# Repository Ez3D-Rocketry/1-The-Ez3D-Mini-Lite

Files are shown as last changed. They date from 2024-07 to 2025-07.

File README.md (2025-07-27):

# The-Ez3D-Mini-Lite

- Great park flyer that uses mini A motors
- Parts tape together
- No glue required

# Parts List:
1. Ez3D-1320 Fin Can
2. BT-20 Nose Cone
3. 13mm Retainer Cap
   - Print out the multiple sizes (No scaling, +3%, +5%), These account for different printing tolerances and post-flight shrinking.
4. Six (6) inches of BT-20 type body tube
   - A standard 18 inch tube makes three kits
   - 3D printable tube cutting guide included in repository files
5. Three (3) feet of Kevlar string for Recovery Harness
   - Flight tested on 9KM DWLIFE Black Braided Kevlar Cord (1.3mm, 300 lb) but others may work
6. Twelve (12) inches of streamer (Optional)
8. Tape

# Assembly: 

**NOTE: Individual printers and filament have different tolerances** <br />
**- Fit check items before assembly and sand to fit if required**
     
1. Tie Recovery Harness to hole in Fin Can
2. Thread Recovery Harness thru Body Tube
3. Slide Body Tube onto top of Fin Can
4. Tape Body Tube to Fin Can - avoid blocking integrated launch lug
5. Tie loose end of Recovery Harness to Nose Cone
6. Tie streamer to Recovery Harness near top of Nose Cone



# Launch Preparation:
1. Insert 1 or 2 squares of recovery wadding into Body Tube
2. Load Recovery Harness and Streamer into Body Tube
3. Place Nose Cone on top of Body Tube - ensure slightly snug fit
4. Slide BT-5 insulator into Fin Can before motor (Optional)
5. Load motor into Fin Can
6. Screw Motor Retention Cap onto base of Fin Can
   - Depending on your printer, the larger sizes may fit better
   - After a flight or two, the smaller size may fit better
7. Launch using standard model rocket procedures

# Recommended motors and expected performance: 

1/2A3-2T or 4T   = 170 ft  (Optimum delay = 2.9 s)

A10-3T               = 370 ft (Optimum delay = 3.5 s)

A3-4T                = 400 ft (Optimum delay = 3.9 s)

# IMPORTANT POST FLIGHT NOTES:
- 3D printed material shrinks after cooling down from heat of motor
- Removal of motor may be difficult or impossible after one or several flights
- The smaller motor retainer cap may fit better after the first flight
- If existing motor retainer caps no longer work, friction or tape may suffice for retention
- PLA filament most suspectable to shrinking. Others may last longer.

## Entire kit fits in a Ziplock sandwich bag!



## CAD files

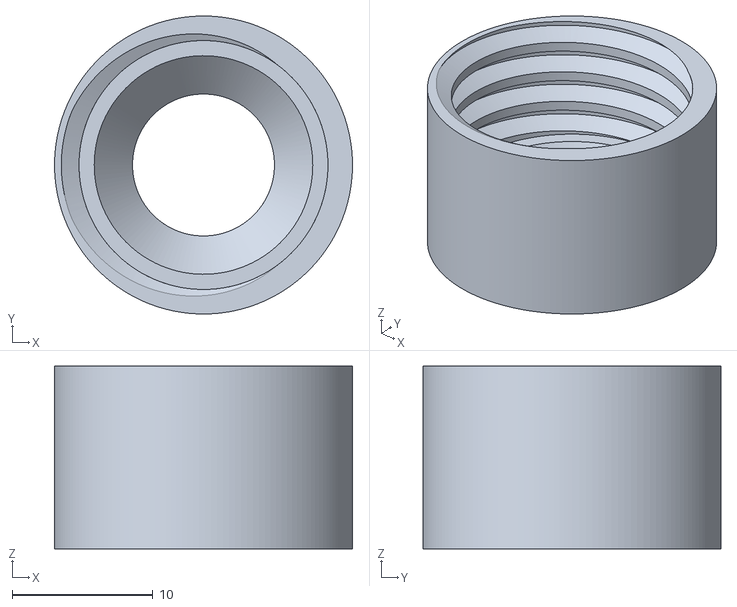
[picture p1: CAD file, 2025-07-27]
3D printing files/13mm Retainer Cap M20x2-13mmTall x1.01in X and Y.stl
21.2 x 21.2 x 13.0

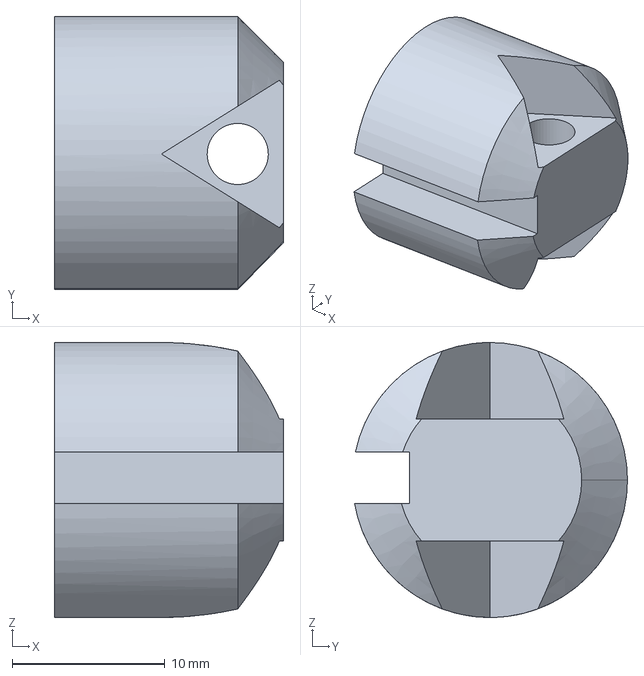
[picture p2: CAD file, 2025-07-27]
FreeCAD Files/BT20 Nose Cone - Elliptical, Solid, with slot.FCStd
15.0 x 17.9 x 18.0 mm

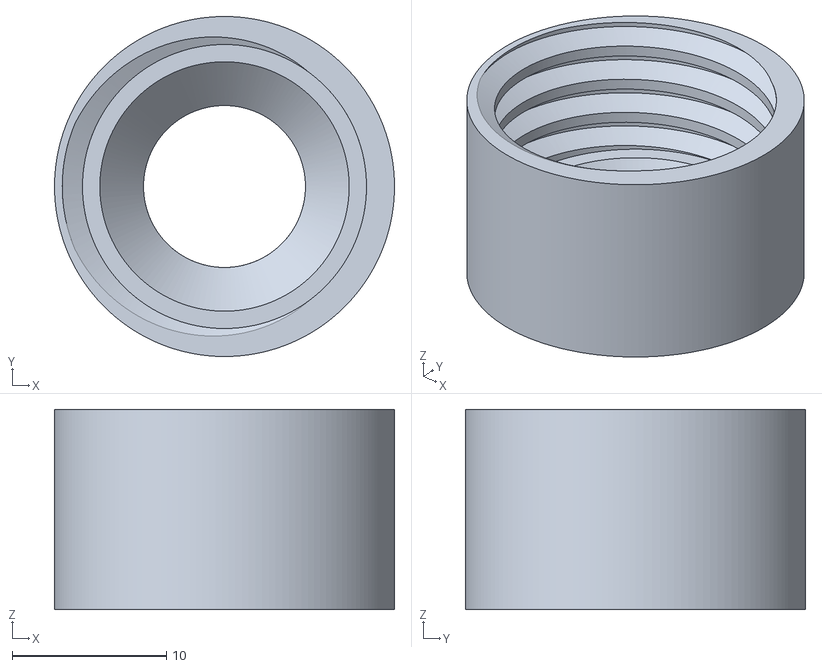
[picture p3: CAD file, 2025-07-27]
3D printing files/13mm Retainer Cap M20x2-13mmTall x1.05 in X and Y.stl
22.0 x 22.0 x 13.0

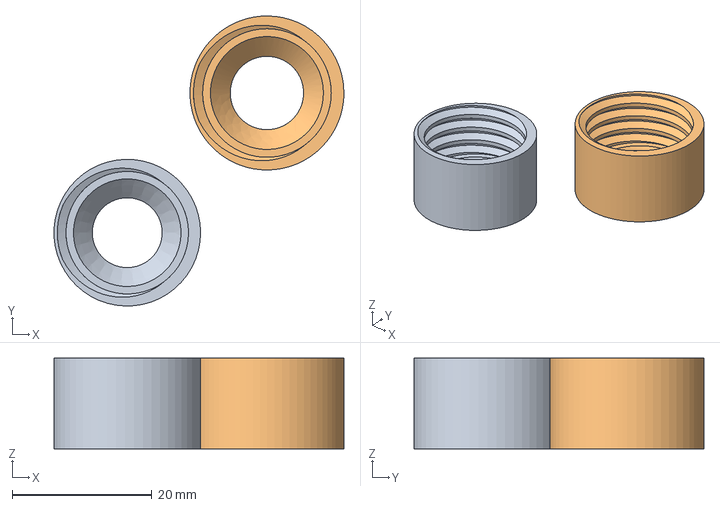
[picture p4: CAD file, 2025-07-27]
FreeCAD Files/13mm Retainer Cap M20x2-13mmTall.FCStd
41.5 x 41.5 x 13.0 mm
Use this Clone to make scaled up versions

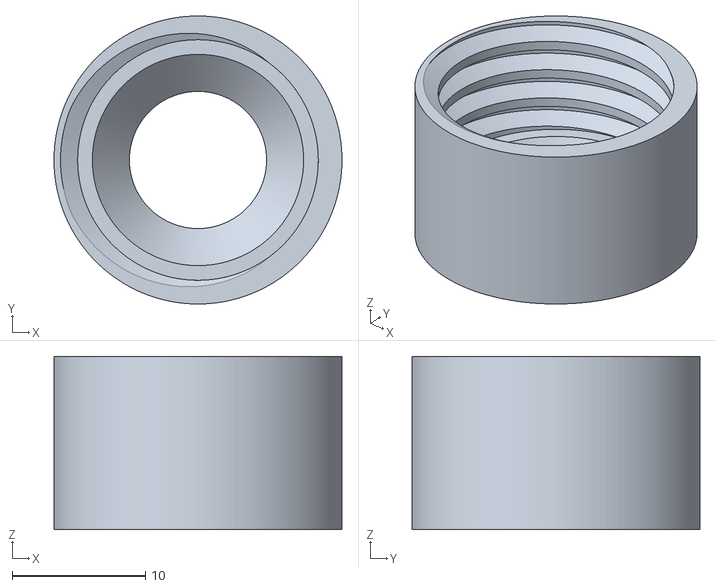
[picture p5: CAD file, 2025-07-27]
3D printing files/13mm Retainer Cap M20x2-13mmTall x1.03 in X and Y.stl
21.6 x 21.6 x 13.0

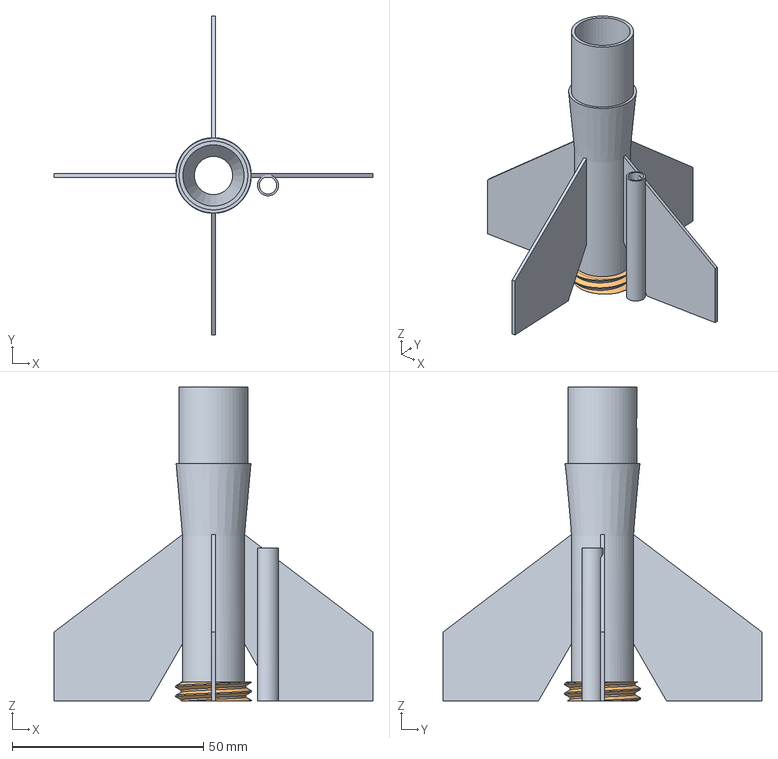
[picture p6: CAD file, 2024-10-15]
FreeCAD Files/Ez3D-1320-4 Fin Can.FCStd
83.5 x 83.5 x 82.1 mm
13mmThread20x2.5-5mmTall

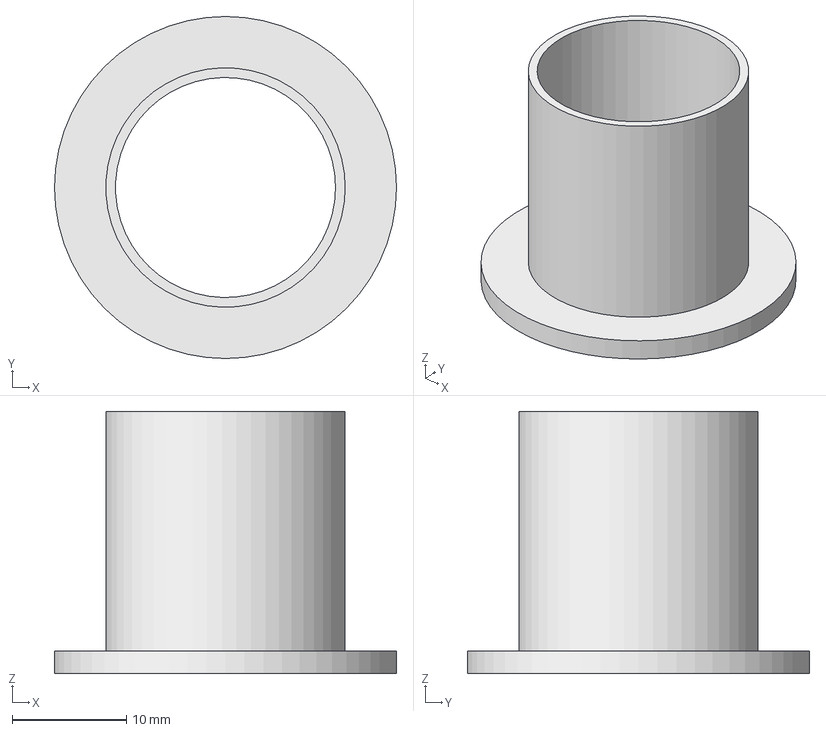
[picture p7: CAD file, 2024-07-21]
FreeCAD Files/BT20 Tube Cutter Guide.FCStd
30.0 x 30.0 x 23.0 mm

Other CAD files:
3D printing files/BT20 Nose Cone - Elliptical, Solid, with slot.stl
3D printing files/BT20 Tube Cutter Guide.stl
3D printing files/Ez3D-1320-4 Fin Can.stl

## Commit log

2024-07-21 Ez3D Mini Lite Fin Can STL File
    [Ez3D Mini Lite Fin Can.stl]
2024-07-21 Mini Lite Fin Can FreeCAD file
    [Ez3D Mini Lite Fin Can.FCStd]
2024-07-21 Mini Lite Fin Can STL file
    [Ez3D Mini Lite Fin Can.stl]
2024-07-21 BT5 Tube Cutter Guide FreeCAD file
    [BT5 Tube Cutter Guide.FCStd]
2024-07-21 BT5 Tube Cutter Guide STL file
    [BT5 Tube Cutter Guide.stl]
2024-07-21 BT20 Tube Cutter Guide FreeCAD file
    [BT20 Tube Cutter Guide.FCStd]
2024-07-21 BT20 Tube Cutter Guide STL file
    [BT20 Tube Cutter Guide.stl]
2024-07-21 BT20 Nose Cone - solid with hole in base - STL file
    [BT20 Nose Cone - solid with threading hole in base.stl]
2024-07-21 BT20 Nose Cone - solid with threading hole in base - FreeCAD file
    [BT20 Nose Cone - solid with threading hole in base.FCStd]
2024-07-21 BT20 Nose Cone - simple attachment - FreeCAD file
    [BT20 Nose Cone with simple threading hole.FCStd]
2024-07-21 BT20 Nose Cone with simple attachment - STL file
    [BT20 Nose Cone with simple threading hole.stl]
2024-08-03 Motor Retainer - Orig Size (smallest)
    [13mm Retainer Cap M20xReg-13mmTall NO scaling.stl]
2024-08-03 13mm motor retainer - orig size (smallest)
    [13mm Retainer Cap original size (smallest).stl]
2024-08-03 motor retainer scaled up 3%
    [13mm Retainer Cap scaled up 3 percent in X and Y.stl]
2024-08-03 motor retainer scaled up 5%
    [13mm Retainer Cap scaled up 5 percent in X and Y.stl]
2024-08-03 motor retainer FreeCAD file
    [13mm Retainer Cap M20xReg-13mmTall label on side.FCStd]
2024-10-13 Fin Can file
    [Ez3D Mini Lite Fin Can.stl]
2024-10-13 moved to folder
    [BT20 Tube Cutter Guide.FCStd]
2024-10-13 Ez3D Mini Lite Fin Can FreeCAD file
    [Ez3D Mini Lite Fin Can.FCStd]
2024-10-13 BT20 Nose Cones
    [BT20 Nose Cone - solid with threading hole in base.stl, BT20 Nose Cone with simple threading hole.stl]
